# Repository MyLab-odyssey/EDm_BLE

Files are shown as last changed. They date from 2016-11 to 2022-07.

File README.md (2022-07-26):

Stand With Ukraine (https://stand-with-ukraine.pp.ua)

# EDm_BLE





Monitor the status of your Smart electric drive EV with the Blynk app.  
**This is a work-in-progress project - more features to come...**

Further documentation in the [Wiki](https://github.com/MyLab-odyssey/EDm_BLE/wiki).

---
## Intention
When driving your electric car the knowledge of the real state of charge (SoC) is essential. The usable range is directly related to the SoC of the battery. Some EVs - like the Smart ED - will hide some Ah for back-up and the displayed SoC is more pessimistic than the real charge would suggest.

In the [ED_BMSdiag project](https://github.com/MyLab-odyssey/ED_BMSdiag) I developed a diagnostics tool for the Smart electric drive EV based on an Arduino UNO with a CAN bus shield. Data is send via a serial USB connection to a laptop.  
In every day use this is not a practical use case, so I searched for an easy solution to display the data on a mobile phone. [The Blynk app](http://www.blynk.cc) is a great way for a very flexible dashboard on iOS and on Android phones.

<p align="center">

<p/>

You can display the content you need and arrange different widgets to show the values. Using gauges, value displays and graphs the app gives you the freedom to select the data you really need.

<p align="center">

<br>
(rearrange widgets or add a graph)<br>
<p/>

Blynk is able to use a bluetooth low energy connection for data transmission. But adding a BLE interface to the Arduino would be only a small step forward. So I decided to develop my own BLE dongle to connect to the OBD port of the car. A system I can leave plugged in while driving and to be energy efficient to stay without depleting the 12V battery. Therefor the RFduino micro controller is the perfect fit as it is small, very efficient and stable. It runs a well developed RTOS and can be programmed with the Arduino IDE. It has excellent ultra low power features for a deep sleep of the module.

## What is Needed
* The PCB: You can use the Eagle CAD files for ordering the PCB at various online manufacturing services. You will find the board on [OSH Park and can order it there](https://oshpark.com/shared_projects/RnRzi1Kz). As an alternative a local FabLab or MakerSpace may has a rapid prototyping mill for PCBs you could use. I made my prototype this way.

* The parts: get the complete bill of materials ([BOM](https://github.com/MyLab-odyssey/EDm_BLE/blob/master/schematics/EDm_v1.1_BOM.txt)) from my GitHub-repo. Most parts are stock articles from common distributors.
You need skills in soldering SMD parts and a good soldering station (the CAN controller is fine pitch).

## Getting started
* Install the [Arduino IDE](https://www.arduino.cc/en/Main/Software) and then follow the instructions for [RFduino installation](https://github.com/RFduino/RFduino/blob/master/README.md#installation).
* Download the Repo and copy it to your Arduino folder. Find detailed instructions in my ED_BMSdiag project ([english](https://github.com/MyLab-odyssey/ED_BMSdiag/wiki/Installation) | [german](https://github.com/MyLab-odyssey/ED_BMSdiag/wiki/Installation_DE)), as it is very similar.
* Using Blynk is described in the Wiki. You can clone my basic project and then modify it. The access token must be copied into the program code and is then compiled for the RFduino.
* Connect the USB to UART adapter and upload the program.
* Remove the USB programmer and plug the dongle into the OBD port of the car. Start Blynk app and connect to the dongle (detailed instructions here).

## Outlook
Currently only live data will be displayed. I will try to port the complete features of the ED_BMSdiag project, so you can use Blynk to get all information about your vehicle.

## Version history
version  | comment
-------- | --------
v0.1.0   | Initial commit with all readouts as in the vehicle dashboard.

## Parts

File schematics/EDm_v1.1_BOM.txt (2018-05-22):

BOM EDm_v1.1

Qty Value                  Device                                                   Package                  Parts             Description / Mouser PartNo.
2                          LED_E                                                    LED_1206                 BLE_LINK, CAN-BUS LED, 859-LTST-C150GKT (green); 859-LTST-C150TBKT (blue)
1   0.01 muF               C-EUC0805                                                C0805                    C1                CAPACITOR
1   100K 1/10W             SMD-RES-100K-5%-1/10W(0603)                              R0603                    R2                RESISTOR
2   100n                   CAP0805                                                  0805                     C4, C5            CAPACITOR
1   120R                   SMD-RES-120R-1%-1/10W(0603)                              R0603                    R4                RESISTOR
1   16MHz                  SMD_OSC2                                                 SMD_OSC_35X15            Q1                RESONATOR, 81-CSTCE16M0V53-R0 (EOL) -> use CSTNE16M0V530000R0 (81-CSTNE16M0V530000R)
4   1K                     SMD-RES-1K-1%-1/10W(0603)                                R0603                    R1, R5, R6, R7    RESISTOR
1   1k                     R-EU_R0603                                               R0603                    R3                RESISTOR
2   22u 16V                CPOL-EUSMCA                                              SMC_A                    C2, C3            POLARIZED CAPACITOR (TANTALUM), 647-F931C226MAA
2   2N7002                 SMD-MOSFET-N-CH-60V-300MA-LOGIC-LEVEL-FET-2N7002(SOT-23) SOT-23                   Q2, Q3            MOSFET, 863-2N7002LT1G
1   2x3p-2.54              DIP-BLACK-FEMALE-HEADER-VERT(2X3P-2.54)                  H2X3-2.54                J2                CONNECTOR
1   500mA, slow            FUSE500MA                                                F3366                    F1                FUSE, 576-0452.500MRL
1   DCDC_OKI-78SR          DCDC_OKI-78SR                                            OKI-78SR                 78SR              5V, 4.95W DC/DC Converter, 580-OKI78SR51.5W36HC
1   ENABLE TRANCEIVER STBY JUMPER-PAD-2-NOYES_SILK                                  PAD-JUMPER-2-NO_YES_SILK JP1
1   MCP1755-3.3V           MCP1755 3.3V version                                     SOT23-5                  IC3               3.3V Microchip MCP1755 LDO Voltage Regulator, 579-MCP1755T-3302EOT
1   MCP2515                MCP2515ST                                                TSSOP20                  IC1               MC2515, 579-MCP2515-I/ST
1   MCP2562                MCP2551SO8                                               SO08                     IC2               CAN Transceiver Microchip, 579-MCP2562-E/SN
1   OBDII                  M08X2-OBDII-COMTECH                                      OBDII-COMTECH            J1                .1" headers, two rows of 8 each
1   PESD2CAN               PESD2CAN                                                 SOT23                    D4                Silicon Schottky Diodes, 771-PESD2CAN-T/R
1   RFD22301               RFD22301                                                 RFD21733                 RFDUINO           RF Digital RFD22301, 975-RFD22301 (EOL)
													     -> use SIMBLEE (975-RFD77101) with adapter(*) or redesign for other MCU
1   SMAJ18CA               DIODESMA                                                 SMA-DIODE                D2                Diode, 576-SMAJ18CA

(*) SIMBLEE to RFDUINO footprint adapter: <https://oshpark.com/shared_projects/TrsQzmnW>

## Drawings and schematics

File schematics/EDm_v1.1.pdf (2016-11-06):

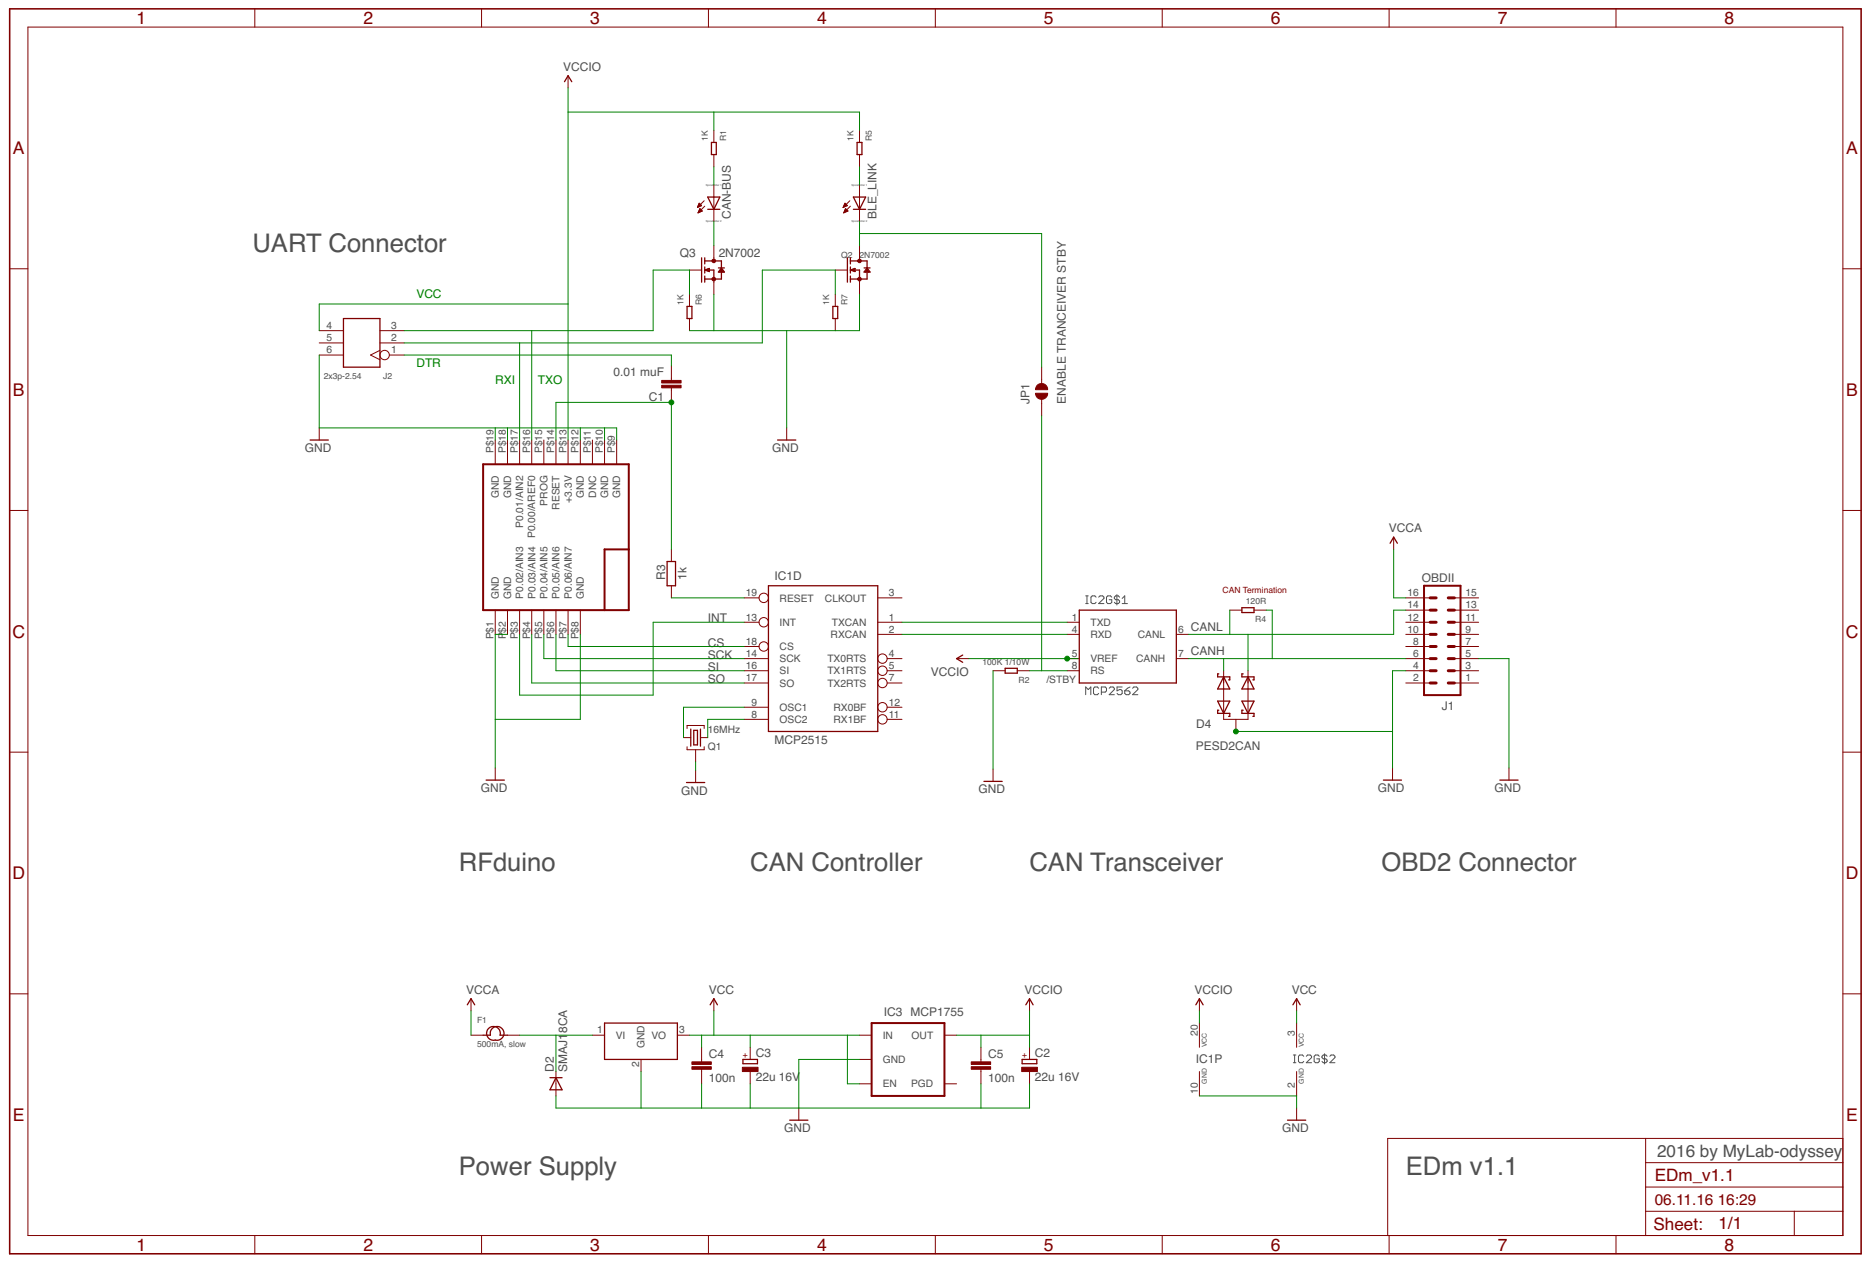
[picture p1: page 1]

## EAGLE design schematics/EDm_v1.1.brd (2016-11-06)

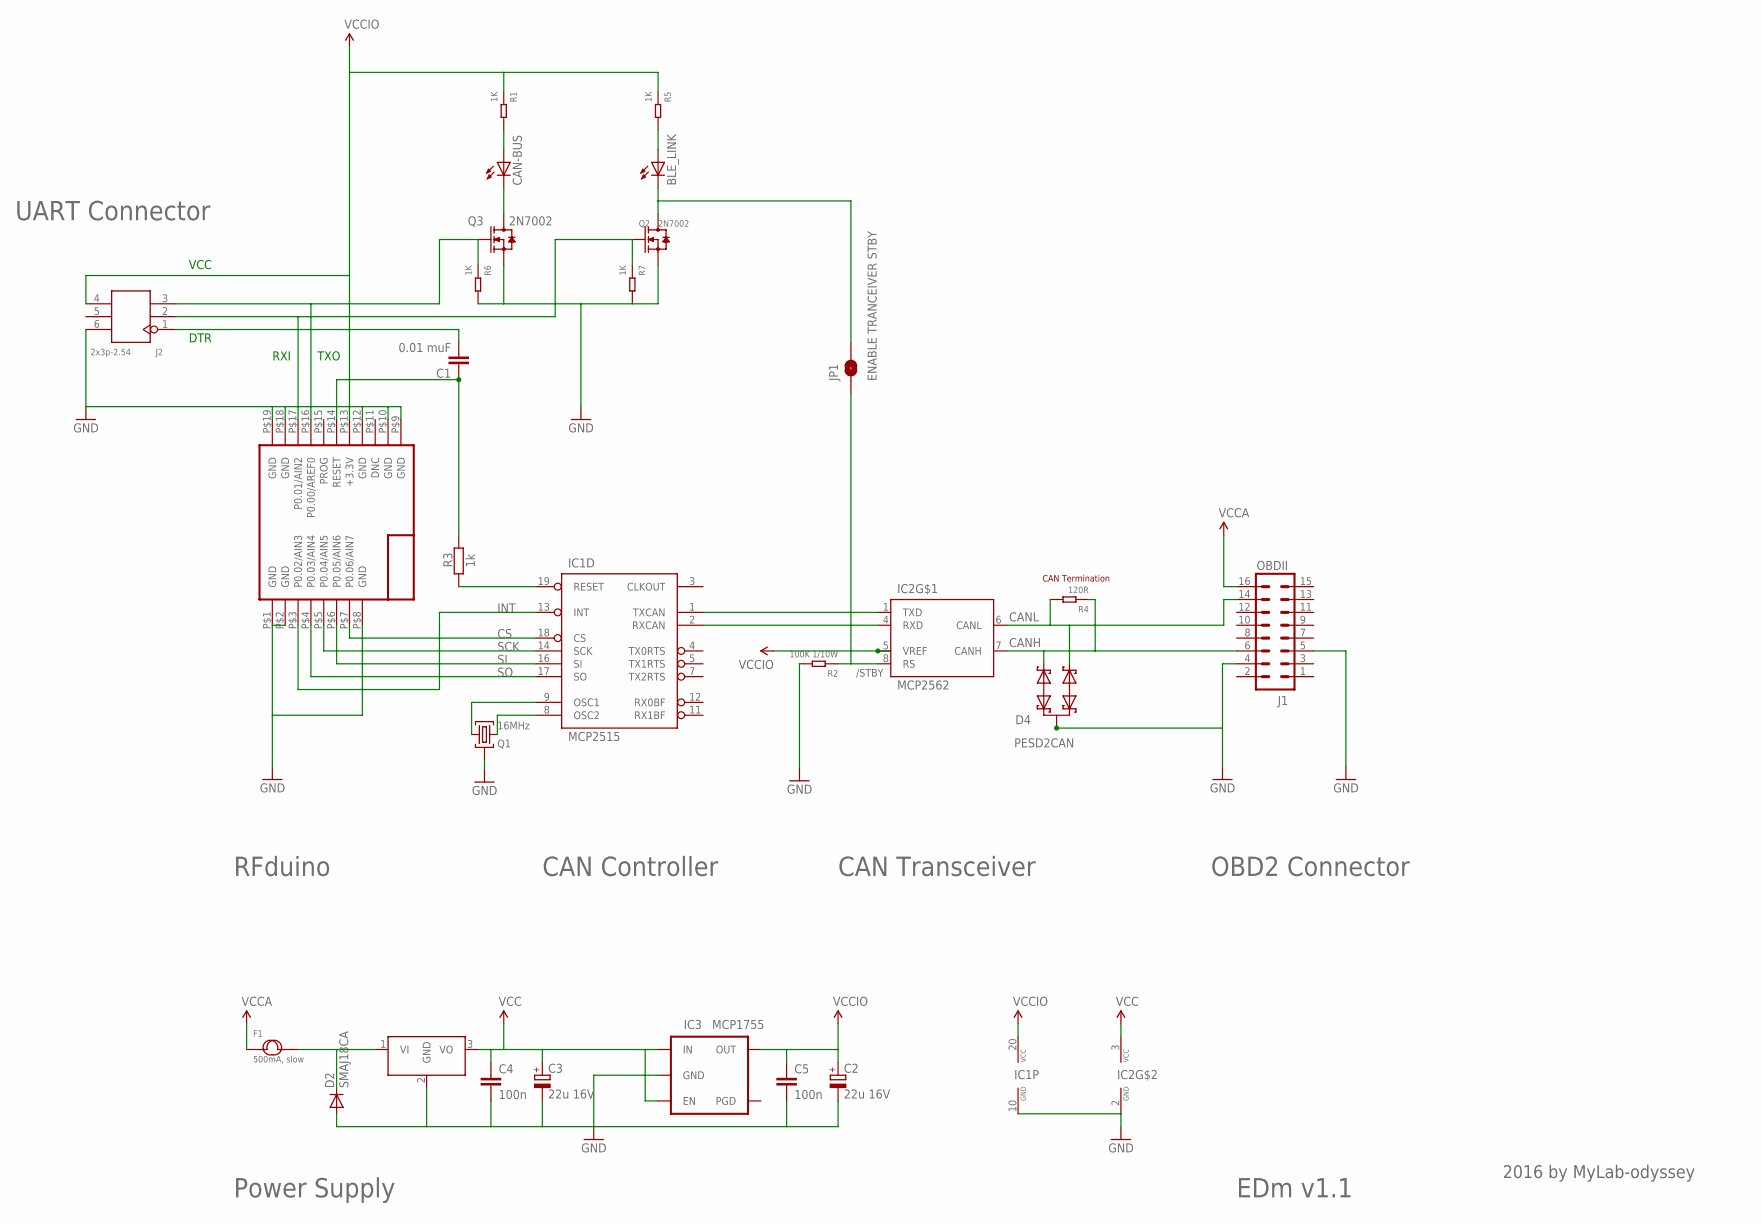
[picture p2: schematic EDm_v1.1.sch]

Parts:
78SR: DCDC_OKI-78SR; OKI-78SRH
BLE_LINK: LED_E; LED_1206
C1: 0.01 muF; C0805
C2, C3: 22u 16V; SMC_A
C4, C5: 100n; 0805
CAN-BUS: LED_E; LED_1206
D2: SMAJ18CA; SMA-DIODE
D4: PESD2CAN; SOT23
F1: 500mA, slow; F3366
IC1: MCP2515; TSSOP20
IC2: MCP2562; SO08
IC3: MCP1755; SOT23-5
J1: OBDII; OBDII-COMTECH; PARTNO OBD-II
J2: 2x3p-2.54; H2X3-2.54
JP1: ENABLE TRANCEIVER STBY; PAD-JUMPER-2-NO_YES_SILK
Q1: 16MHz; SMD_OSC_35X15
Q2, Q3: 2N7002; SOT-23
R1, R5, R6, R7: 1K; R0603
R2: 100K 1/10W; R0603
R3: 1k; R0603
R4: 120R; R0603
RFDUINO: RFD22301; RFD21733

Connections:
CANH: D4.1, IC2.7 (CANH), J1.6, R4.1
CANL: D4.2, IC2.6 (CANL), J1.14, R4.2
CAN_RX: IC1.2 (RXCAN), IC2.4 (RXD)
CAN_TX: IC1.1 (TXCAN), IC2.1 (TXD)
CS: IC1.18 (CS), RFDUINO.P$7 (P0.06/AIN7)
GND: 78SR.2 (GND), C2.-, C3.-, C4.2, C5.2, D2.A, D4.3, IC1.10 (GND), IC2.2 (GND), IC3.2 (GND), J1.4, J1.5, J2.6, Q1.GND, Q2.2 (S), Q3.2 (S), R2.2, R6.2, R7.2, RFDUINO.P$1 (GND), RFDUINO.P$2 (GND), RFDUINO.P$8 (GND), RFDUINO.P$9 (GND), RFDUINO.P$10 (GND), RFDUINO.P$12 (GND), RFDUINO.P$18 (GND), RFDUINO.P$19 (GND)
INT: IC1.13 (INT), RFDUINO.P$3 (P0.02/AIN3)
unnamed: IC1.19 (RESET), R3.2
unnamed: C1.1, R3.1, RFDUINO.P$14 (RESET)
unnamed: J2.3, Q3.1 (G), R6.1, RFDUINO.P$16 (P0.00/AREF0)
unnamed: J2.2, Q2.1 (G), R7.1, RFDUINO.P$17 (P0.01/AIN2)
unnamed: C1.2, J2.1
unnamed: CAN-BUS.C, Q3.3 (D)
unnamed: CAN-BUS.A, R1.2
unnamed: BLE_LINK.A, R5.2
unnamed: BLE_LINK.C, JP1.2, Q2.3 (D)
unnamed: IC2.8 (RS), JP1.1, R2.1
unnamed: 78SR.1 (VI), D2.C, F1.2
OSC1: IC1.9 (OSC1), Q1.1
OSC2: IC1.8 (OSC2), Q1.2
SCK: IC1.14 (SCK), RFDUINO.P$5 (P0.04/AIN5)
SI: IC1.16 (SI), RFDUINO.P$6 (P0.05/AIN6)
SO: IC1.17 (SO), RFDUINO.P$4 (P0.03/AIN4)
VCC: 78SR.3 (VO), C3.+, C4.1, IC2.3 (VCC), IC3.1 (IN), IC3.3 (EN)
VCCA: F1.1, J1.16
VCCIO: C2.+, C5.1, IC1.20 (VCC), IC2.5 (VREF), IC3.5 (OUT), J2.4, R1.1, R5.1, RFDUINO.P$13 (+3.3V)

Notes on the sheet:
CAN Termination
CAN Controller
CAN Transceiver
/STBY
OBD2 Connector
RFduino
UART Connector
Power Supply
EDm v1.1
2016 by MyLab-odyssey
VCC
TXO
RXI
DTR

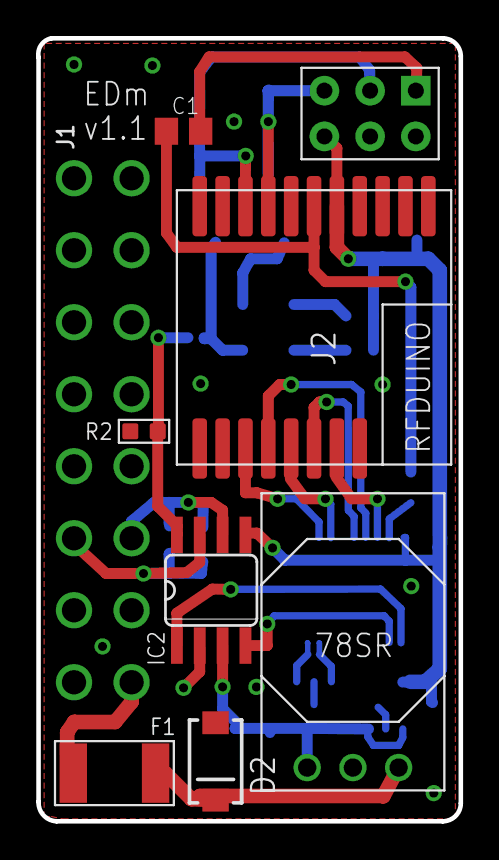
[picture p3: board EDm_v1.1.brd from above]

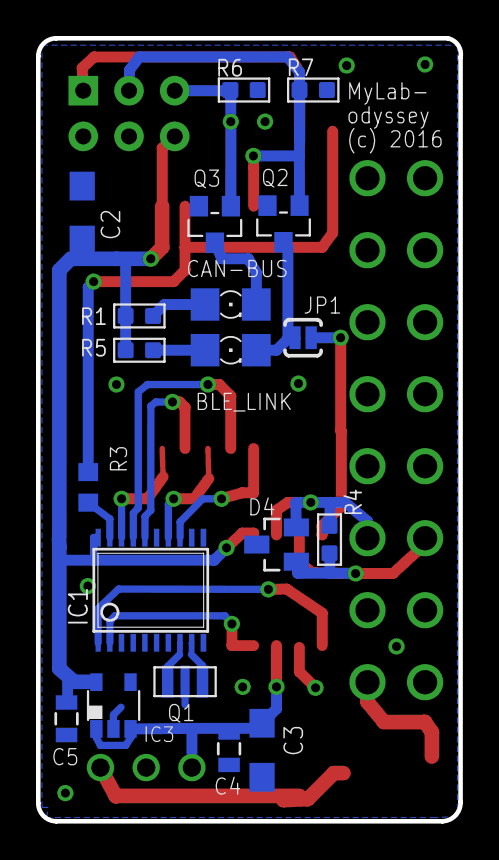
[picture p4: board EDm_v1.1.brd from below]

Board: 2 copper layers, 23.5 x 43.5 mm, 28 parts (19 on the bottom side), 26 nets.

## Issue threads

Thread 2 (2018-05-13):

FYI: end–of–life for components

cdn, 2018-05-13:
[Mouser listing](https://www.mouser.co.uk/ProductDetail/RF-Digital-Wireless/RFD22301) for RFduino states its EOL this year (2018).

cdn, 2018-05-22:
Same applies to the resonator: CSTCE16M0V53-R0

MyLab-odyssey, 2018-05-22:
Thanks for the info! Nothing is designed to last ;-) The resonator production started in 2000, but Murata lists a recommended alternative: [CSTNE16M0V530000R0](https://www.murata.com/products/productdetail?partno=CSTNE16M0V530000R0) same specs but with better temperature range.

Also the RFduino is quite old and HEPTAGON released the Simblee about three years ago. It is very compatible regarding basic RFduino features and there is a OSHpark project for an [adapter board](https://oshpark.com/shared_projects/TrsQzmnW).

I updated the BOM for those components.

cdn, 2018-05-22:
Can you confirm the Microchip MCP1755 LDO Voltage Regulator is the 5V version? The chip(s) it supplies appear to require 3.3V.

MyLab-odyssey, 2018-05-22:
Uuups. This is a nasty typo! THX for the comment as VCCIO is indeed 3.3V and you have to use the appropriate variant: [MCP1755T-3302E/OT](https://www2.mouser.com/ProductDetail/Microchip-Technology/MCP1755T-3302E-OT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)

Closed 2018-05-22.

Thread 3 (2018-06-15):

Smart 451 300km Range

JonCRD, 2018-06-15:
Hello,
My name is Jonathan Cuillerier and I am the owner of CRD. We rent out Smart ED 451 for Students in major universities in Canada.

I have been looking at what you have accomplished for the Smart 451 & 453 CAN Bus and find it impressive. I would like to have a conversation with you as I am looking for someone with your skill set to advance our Battery upgrade project (250 to 300km for the 451, Additional 11.6KWh) and 22KW charger 240V upgrade  (1h full charge,240VAC instead of the 400V 3phase from Europe). my email is jonathan@crd.tech and would love to hear more about you and your background.

Cheers,
Jonathan

P.S. Sry for passing thru the issue section but I did not know any other way to contact you.

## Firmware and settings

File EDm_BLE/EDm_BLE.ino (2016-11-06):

//--------------------------------------------------------------------------------
// EDm_BLE, v0.1.0
// Retrieve battery diagnostic data from your smart electric drive EV.
//
// (c) 2016 by MyLab-odyssey
//
// Licensed under "MIT License (MIT)", see license file for more information.
//
// THIS SOFTWARE IS PROVIDED BY THE COPYRIGHT HOLDER OR CONTRIBUTORS "AS IS" AND
// ANY EXPRESS OR IMPLIED WARRANTIES, INCLUDING, BUT NOT LIMITED TO, THE IMPLIED
// WARRANTIES OF MERCHANTABILITY AND FITNESS FOR A PARTICULAR PURPOSE ARE
// DISCLAIMED. IN NO EVENT SHALL THE COPYRIGHT HOLDER OR CONTRIBUTORS BE LIABLE FOR
// ANY DIRECT, INDIRECT, INCIDENTAL, SPECIAL, EXEMPLARY, OR CONSEQUENTIAL DAMAGES
// (INCLUDING, BUT NOT LIMITED TO, PROCUREMENT OF SUBSTITUTE GOODS OR SERVICES;
// LOSS OF USE, DATA, OR PROFITS; OR BUSINESS INTERRUPTION) HOWEVER CAUSED AND ON
// ANY THEORY OF LIABILITY, WHETHER IN CONTRACT, STRICT LIABILITY, OR TORT
// (INCLUDING NEGLIGENCE OR OTHERWISE) ARISING IN ANY WAY OUT OF THE USE OF THIS
// SOFTWARE, EVEN IF ADVISED OF THE POSSIBILITY OF SUCH DAMAGE.
//--------------------------------------------------------------------------------
//! \file    EDm_BLE.ino
//! \brief   Retrieve data from your smart electric drive EV.
//! \brief   Using a RFduino micro controller and the Bynk app for display
//! \brief   www.rfduino.com, www.blynk.cc
//! \date    2016-November
//! \author  MyLab-odyssey
//! \version 0.1.0
//--------------------------------------------------------------------------------

//#define BLYNK_DEBUG
//#define BLYNK_PRINT Serial

#define BLYNK_USE_DIRECT_CONNECT
//#define BLYNK_MAX_SENDBYTES 256 // Default is 128

#include <BlynkSimpleRFduinoBLE.h>
#include <RFduinoBLE.h>
#include <String.h>
#include "canDiag.h"

#define CS     10                //!< chip select pin of MCP2515 CAN-Controller
#define CS_SD  8                 //!< CS for SD card, if you plan to use a logger...
MCP_CAN CAN0(SS);                //!< Set CS pin

canDiag DiagCAN;
BatteryDiag_t BMS;
ChargerDiag_t NLG6;
CoolingSub_t CLS;
DriveStats_t DRV;

CTimeout CAN_Timeout(1000);     //!< Timeout value for CAN response in millis
CTimeout Terminal_Timeout(1000);
CTimeout DEVstatus_Timeout(3000);

CTimeout DRV_Timeout(5000);
CTimeout BMS_Timeout(2500);

//#define BLYNK_SEND_THROTTLE 20

WidgetLED LEDcon(V0);
//WidgetTerminal terminal(V12);

//unsigned long time = millis();
unsigned long IOcount = 0;
unsigned int delta = 0;

// You should get Auth Token in the Blynk App.
// Go to the Project Settings (nut icon).
char auth[] = "put your auth token here";

int state = 0;
int rssi = 0;
boolean fConnected = false;
byte taskSOC = 1;
byte taskPower = 1;
boolean fOK_SOC = false;
boolean fOK_Power = false;
byte failCount = 0;

int tab_index = 0;

//--------------------------------------------------------------------------------
//! \brief   SETUP()
//--------------------------------------------------------------------------------
void setup() {
  //Serial.begin(9600);
  //while(!Serial);

  //LED CAN-Bus active
  pinMode(0, OUTPUT);
  //LED BLE connected
  pinMode(1, OUTPUT);

  // MCP2515 read buffer: setting pin 2 for input, LOW if CAN messages are received
  pinMode(2, INPUT);

  // Initialize MCP2515 and clear filters
  DiagCAN.begin(&CAN0, &CAN_Timeout);
  DiagCAN.clearCAN_Filter();

  connectRFDuino();
  Serial.println("Waiting for connections...");

  /*while ((fConnected = Blynk.connect()) == false) {
    // Wait until connected
  }*/

}

//--------------------------------------------------------------------------------
//! \brief   LOOP()
//--------------------------------------------------------------------------------
void loop() { 
  Blynk.run();
  if (state && fConnected && DRV_Timeout.Expired(true)) {
    state = DiagCAN.ReadCAN(&DRV, 0);
  }
  Blynk.run();
  if (state && fConnected && BMS_Timeout.Expired(true)) {
    state = DiagCAN.ReadCAN(&BMS, 0);
  }
  Blynk.run();
  if (DEVstatus_Timeout.Expired(true)) {
    DEVstatus();
  }
}

void connectRFDuino () {
  RFduinoBLE.deviceName = "RFDuino";
  RFduinoBLE.advertisementInterval = MILLISECONDS(300);
  RFduinoBLE.txPowerLevel = 0;  // (-20dbM to +4 dBm)

  // start the BLE stack
  RFduinoBLE.begin();
  Blynk.begin(auth);
}

//--------------------------------------------------------------------------------
//! \brief   Read SOC values
//! \brief   Trigger on a virtual pin from Blynk app, set frequency in app
//! \param   selected virtual pin, CONST from Blynk library
//--------------------------------------------------------------------------------
BLYNK_READ(V1) {
  ReadValues_SOC();
  //Serial.print("SOC: "); Serial.println(BMS.SOC);
  //Blynk.virtualWrite(V1, BMS.SOC);
}

//--------------------------------------------------------------------------------
//! \brief   Read Power values (voltage, amps, calculate power)
//! \brief   Trigger on a virtual pin from Blynk app, set frequency in app
//! \param   selected virtual pin, CONST from Blynk library
//--------------------------------------------------------------------------------
BLYNK_READ(V3) {
  ReadValues_Power();
}

//--------------------------------------------------------------------------------
//! \brief   Read LV value, voltage from 12V battery
//! \brief   Trigger on a virtual pin from Blynk app, set frequency in app
//! \param   selected virtual pin, CONST from Blynk library
//--------------------------------------------------------------------------------
BLYNK_READ(V6) {
  if(state) Blynk.virtualWrite(V6, BMS.LV);
}

//--------------------------------------------------------------------------------
//! \brief   Read ODO value
//! \brief   Trigger on a virtual pin from Blynk app, set frequency in app
//! \param   selected virtual pin, CONST from Blynk library
//--------------------------------------------------------------------------------
BLYNK_READ(V7) {
  if(state) Blynk.virtualWrite(V7, BMS.ODO);
  //Serial.print("ODO, "); Serial.println(state);
}

//--------------------------------------------------------------------------------
//! \brief   Read ECO values
//! \brief   Trigger on a virtual pin from Blynk app, set frequency in app
//! \param   selected virtual pin, CONST from Blynk library
//--------------------------------------------------------------------------------
BLYNK_READ(V21) {
  //state = DiagCAN.ReadECO(&DRV);
  //delay(100);
  if(state) Blynk.virtualWrite(V21, DRV.ECO_total);
  if(state) Blynk.virtualWrite(V22, DRV.ECO_accel);
  if(state) Blynk.virtualWrite(V23, DRV.ECO_const);
  if(state) Blynk.virtualWrite(V24, DRV.ECO_coast);
  //Serial.print("ECO, "); Serial.println(state);
}

//--------------------------------------------------------------------------------
//! \brief   Read available power (three stages 99, 66, 33, zero %)
//! \brief   Trigger on a virtual pin from Blynk app, set frequency in app
//! \param   selected virtual pin, CONST from Blynk library
//--------------------------------------------------------------------------------
BLYNK_READ(V25) {
  if(state) Blynk.virtualWrite(V25, DRV.range);
  if(state) {
    String _usablePower ="";
    switch (DRV.usablePower) {
      case 99:
        _usablePower ="> > >";
        break;
      case 66:
        _usablePower ="> >";
        break;
      case 33:
        _usablePower =">";
        break;
      default:
         _usablePower ="- - -";
        break;
    }
    Blynk.virtualWrite(V27, _usablePower);
  }
  //Serial.print("Range, "); Serial.println(state);
}

//--------------------------------------------------------------------------------
//! \brief   Read enery consumption / 100km values, two counters
//! \brief   Trigger on a virtual pin from Blynk app, set frequency in app
//! \param   selected virtual pin, CONST from Blynk library
//--------------------------------------------------------------------------------
BLYNK_READ(V28) {
  //state = DiagCAN.ReadEnergyConsumption(&DRV); 
  //state = true;
  //delay(100);
  if(state) Blynk.virtualWrite(V28, DRV.energyStart /100.0);
  if(state) Blynk.virtualWrite(V29, DRV.energyReset /100.0);
  //Serial.print("Energy, "); Serial.println(state);
}

//--------------------------------------------------------------------------------
//! \brief   Read ODO counters from start and from custom reset
//! \brief   Trigger on a virtual pin from Blynk app, set frequency in app
//! \param   selected virtual pin, CONST from Blynk library
//--------------------------------------------------------------------------------
BLYNK_READ(V30) {
  //state = DiagCAN.ReadUserCounter(&DRV);
  //state = true;
  //delay(100);
  if(state) Blynk.virtualWrite(V30, DRV.odoStart / 10.0);
  if(state) Blynk.virtualWrite(V31, DRV.odoReset / 10.0);
  //Serial.print("UserCounter, "); Serial.println(state);
}

//--------------------------------------------------------------------------------
//! \brief   Uptime counter, for development and to test Blynk connection
//! \brief   Trigger on a virtual pin from Blynk app, set frequency in app
//! \param   selected virtual pin, CONST from Blynk library
//--------------------------------------------------------------------------------
BLYNK_READ(V10) {
  Blynk.virtualWrite(V10, IOcount);
  Serial.println(IOcount++);
  //Serial.print("UptimeCounter, "); Serial.println(state);
  Blynk.virtualWrite(V2, BMS.realSOC / 10.0);
}

//--------------------------------------------------------------------------------
//! \brief   Trigger from virtual button, for development and test
//! \param   selected virtual pin, CONST from Blynk library
//--------------------------------------------------------------------------------
BLYNK_WRITE(V15) {
  int pinData = param.asInt();
  if (pinData == 0) {
    /*for (byte n = 1; n < 94; n++) {
      terminal.print("#"); terminal.print(n);
      terminal.println(": 3885 mV, 19142 As/10");
      delay(100);
      terminal.flush();
      Blynk.run();
    }*/
    DiagCAN.WakeUp();
  }
}

//--------------------------------------------------------------------------------
//! \brief   Sync widget values on first Blynk connection
//--------------------------------------------------------------------------------
BLYNK_CONNECTED() {
  Blynk.syncAll();
}

//--------------------------------------------------------------------------------
//! \brief   Show status of CAN-Bus and Blynk connect
//--------------------------------------------------------------------------------
void DEVstatus() {
  //long ts = millis();
  
  fConnected = Blynk.connected();
  if (!state || !fConnected) { //fConnected
      state = DiagCAN.ClearReadBuffer();
  }
  
  if (!state && failCount < 2) {
    failCount++;
    state = true;
  } else if (failCount > 2) {
    state = false;
    failCount = 0;   
  } else if (state && failCount > 0) {
    failCount--;
    state = true;
  }
  
  Serial.print(state); Serial.print(", "); Serial.println(failCount);
  digitalWrite(0, state);

  if (fConnected) {
    LEDcon.setValue(state * 255); 
    Blynk.virtualWrite(V26, String(DRV.HVactive, BIN)); 
    Blynk.virtualWrite(V11, rssi);
    Blynk.virtualWrite(V9, RFduino_temperature(CELSIUS));
    digitalWrite(1, true);
  } else {
    digitalWrite(1, false);
  }
}

//--------------------------------------------------------------------------------
//! \brief   Callback to return signal strength (RX level -0dBm to -127dBm)
//--------------------------------------------------------------------------------
void RFduinoBLE_onRSSI(int _rssi) {
  rssi = _rssi; 
}

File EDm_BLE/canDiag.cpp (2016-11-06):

//--------------------------------------------------------------------------------
// (c) 2016 by MyLab-odyssey
//
// Licensed under "MIT License (MIT)", see license file for more information.
//
// THIS SOFTWARE IS PROVIDED BY THE COPYRIGHT HOLDER OR CONTRIBUTORS "AS IS" AND
// ANY EXPRESS OR IMPLIED WARRANTIES, INCLUDING, BUT NOT LIMITED TO, THE IMPLIED
// WARRANTIES OF MERCHANTABILITY AND FITNESS FOR A PARTICULAR PURPOSE ARE
// DISCLAIMED. IN NO EVENT SHALL THE COPYRIGHT HOLDER OR CONTRIBUTORS BE LIABLE FOR
// ANY DIRECT, INDIRECT, INCIDENTAL, SPECIAL, EXEMPLARY, OR CONSEQUENTIAL DAMAGES
// (INCLUDING, BUT NOT LIMITED TO, PROCUREMENT OF SUBSTITUTE GOODS OR SERVICES;
// LOSS OF USE, DATA, OR PROFITS; OR BUSINESS INTERRUPTION) HOWEVER CAUSED AND ON
// ANY THEORY OF LIABILITY, WHETHER IN CONTRACT, STRICT LIABILITY, OR TORT
// (INCLUDING NEGLIGENCE OR OTHERWISE) ARISING IN ANY WAY OUT OF THE USE OF THIS
// SOFTWARE, EVEN IF ADVISED OF THE POSSIBILITY OF SUCH DAMAGE.
//--------------------------------------------------------------------------------
//! \file    canDiag.cpp
//! \brief   Library module for retrieving diagnostic data.
//! \date    2016-November
//! \author  MyLab-odyssey
//! \version 0.5.0
//--------------------------------------------------------------------------------
#include "canDiag.h"

//--------------------------------------------------------------------------------
//! \brief   Standard constructor / destructor
//--------------------------------------------------------------------------------
canDiag::canDiag() {
}

canDiag::~canDiag() {  
  delete[] data;
}

//--------------------------------------------------------------------------------
//! \brief   Manage memory for cell statistics
//--------------------------------------------------------------------------------
void canDiag::reserveMem_CellVoltage() {
  CellVoltage.init(CELLCOUNT);
}

void canDiag::reserveMem_CellCapacity() {
  CellCapacity.init(CELLCOUNT);
}

void canDiag::freeMem_CellVoltage() {
  CellVoltage.freeMem();
}

void canDiag::freeMem_CellCapacity() {
  CellCapacity.freeMem();
}

//--------------------------------------------------------------------------------
//! \brief   Memory available between Heap and Stack, works only on UNO!
//--------------------------------------------------------------------------------
int canDiag::_getFreeRam() {
  extern int __heap_start, *__brkval;
  int v;
  return (int) &v - (__brkval == 0 ? (int) &__heap_start : (int) __brkval);
}

//--------------------------------------------------------------------------------
//! \brief   Get method for CellVoltages
//--------------------------------------------------------------------------------
uint16_t canDiag::getCellVoltage(byte n) {
  return CellVoltage.get(n);
}

//--------------------------------------------------------------------------------
//! \brief   Get method for CellCapacities
//--------------------------------------------------------------------------------
uint16_t canDiag::getCellCapacity(byte n) {
  return CellCapacity.get(n);
}

//--------------------------------------------------------------------------------
//! \brief   Initialize CAN-Object and MCP2515 Controller
//--------------------------------------------------------------------------------
void canDiag::begin(MCP_CAN *_myCAN, CTimeout *_myCAN_Timeout) {
  //Set Pointer to MCP_CANobj
  myCAN0 = _myCAN;
  myCAN_Timeout = _myCAN_Timeout;
  
  // Initialize MCP2515 running at 16MHz with a baudrate of 500kb/s and the masks and filters enabled.
  if(myCAN0->begin(MCP_STD, CAN_500KBPS, MCP_16MHZ) == CAN_OK) DEBUG_UPDATE(F("MCP2515 Init Okay!!\r\n"));
  else DEBUG_UPDATE(F("MCP2515 Init Failed!!\r\n"));

  this->data = new byte[DATALENGTH];
}

//--------------------------------------------------------------------------------
//! \brief   Clear CAN ID filters.
//--------------------------------------------------------------------------------
void canDiag::clearCAN_Filter(){
  myCAN0->init_Mask(0, 0, 0x00000000);
  myCAN0->init_Mask(1, 0, 0x00000000);
  //delay(100);
  myCAN0->setMode(MCP_NORMAL);                     // Set operation mode to normal so the MCP2515 sends acks to received data.
}

//--------------------------------------------------------------------------------
//! \brief   Set all filters to one CAN ID.
//--------------------------------------------------------------------------------
void canDiag::setCAN_Filter(unsigned long filter){
  this->respID = filter;
  filter = filter << 16;
  myCAN0->init_Mask(0, 0, 0x07FF0000);
  myCAN0->init_Mask(1, 0, 0x07FF0000);
  myCAN0->init_Filt(0, 0, filter);
  myCAN0->init_Filt(1, 0, filter);
  myCAN0->init_Filt(2, 0, filter);
  myCAN0->init_Filt(3, 0, filter);
  myCAN0->init_Filt(4, 0, filter);
  myCAN0->init_Filt(5, 0, filter);
  //delay(100);
  myCAN0->setMode(MCP_NORMAL);                     // Set operation mode to normal so the MCP2515 sends acks to received data.
}


void canDiag::setCAN_Filter_DRV(){
  myCAN0->init_Mask(0, 0, 0x07FF0000);
  myCAN0->init_Mask(1, 0, 0x07FF0000);
  myCAN0->init_Filt(0, 0, (0x200 << 16));
  myCAN0->init_Filt(1, 0, (0x318 << 16));
  myCAN0->init_Filt(2, 0, (0x3CE << 16));
  myCAN0->init_Filt(3, 0, (0x3F2 << 16));
  myCAN0->init_Filt(4, 0, (0x3D7 << 16));
  myCAN0->init_Filt(5, 0, (0x504 << 16));
  //delay(100);
  myCAN0->setMode(MCP_NORMAL);                     // Set operation mode to normal so the MCP2515 sends acks to received data.
}

//--------------------------------------------------------------------------------
//! \brief   Set request CAN ID and response CAN ID for get functions
//--------------------------------------------------------------------------------
void canDiag::setCAN_ID(unsigned long _respID) {
  if(this->respID != _respID) {
    this->setCAN_Filter(_respID);
  }
  this->respID = _respID;
}
void canDiag::setCAN_ID(unsigned long _rqID, unsigned long _respID) {
  rqID = _rqID;
  if(this->respID != _respID) {
    this->setCAN_Filter(_respID);
  }
  this->respID = _respID; 
}

//--------------------------------------------------------------------------------
//! \brief   Try to wakeup EV CAN bus ***experimental and not working right now!***
//--------------------------------------------------------------------------------
boolean canDiag::WakeUp(){    
  //--- Send WakeUp Pattern ---
  DEBUG_UPDATE(F("Send WakeUp Request\n\r"));
  myCAN0->sendMsgBuf(0x423, 0, 7, rqWakeUp);    // send data: Request diagnostics data, 423!, 452?, 236?
  return true;
}
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

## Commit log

2016-11-06 Added link to PCB @OSH park
2018-05-22 Updated BOM as some parts are EOL (end–of–life)
    Alternatives for resonator and RFduino listed.
2018-05-22 EDIT: use 3.3V variant of MCP1755 !
    THX to comment by cdn!

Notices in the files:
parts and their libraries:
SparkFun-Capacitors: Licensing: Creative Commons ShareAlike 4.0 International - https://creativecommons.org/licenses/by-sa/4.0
